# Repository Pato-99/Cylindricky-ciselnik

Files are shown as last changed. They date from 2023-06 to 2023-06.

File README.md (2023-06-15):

# Cylindrický číselník

Showcase

Mechanický cylindrický číselník je obdoba takzvaných "flip-clock" s tím,
že místo "flipujících" dlaždiček se otáčejí cylindry (válce). Díky tomu je možné
otáčet číselníkem na obě strany a také je ho možné umístit v jakékoliv poloze,
protože ke změně čísel není potřeba gravitace tak jako u "flip-clock".

## Klíčové vlastnosti

- modularita
- jednoduché rozhraní
- asynchronní ovládání jednotlivých válců

## Ovládání/Rozhraní

Číselník lze ovládat pomocí jednoduchých příkazů přes UART nebo MQTT

| Příkaz | Popis |
|---|---|
| `SHOW <int>` | Zobrazí dané číslo. Pokud je počet číslic větší než počet cylindrů, tak se ořízne zprava. |
| `SHOWF <float> <n>` | Zobrazí float na n desetinných míst. Případně se číslo ořízne zprava. |
| `INFO` | Vypíše info jaké číslo je právě zobrazováno a stavy motorů. |
| `CONFIGURE` | Spustí konfigurační mód. |

### Konfigurační mód

Pomocí posílání číslovek (`1, 2, 3, 4, 5, 6, ...`) se po jednotlivých krocích nastaví motory tak,
aby displej ukazoval samé nuly. Potom posláním `s` nastavení uložíme.

Nastavení je poté uloženo ve flash paměti zařízení a tak zůstává zachováno
i po rebootu.

## Implementace SW

K implementaci SW byl použit programovací jazyk MicroPython.

Program se skládá ze 2 hlavních částí:

1. Zpracování vstupu
2. Driver displeje/motorů

V samotné implementaci driveru byly použity 3 úrovně abstrakce.

1. Driver samotného unipolárního krokového motoru
2. Driver jednotlivých cylindrů (motor, převod, logika zobrazování číslic)
3. Driver displeje jako celku (skládá se z cylindrů)

### Asynchronní ovládání

Ovládání jednotlivých motorů je řešeno asynchronně pomocí knihovny `uasyncio`.

Asynchronní programování se hodí použít tam, kde jsou procedury takzvaně "I/O bound.
To znamená, že většinu času běhu procedury zabírá čekání například na vstup,
na navázání spojení atd. V našem případě je to čekání mezi jednotlivými kroky
krokového motoru. Myšlenkou je využití tohoto času pro něco užitečnějšího.
Díky tomu můžeme dosáhnout určité míry paralelismu za použití jen jednoho
vlákna.

Základem jsou klíčová slova `async` a `await`.

Připsáním klíčového slova `async` před deklaraci funkce říkáme, že se jedná
o takzvanou **courutine** a že se o její běh bude starat uasyncio. Coroutines 
je možné volat z jiných coroutines za použítí klíčového slova `await` nebo
předáním jako parametr funkcím z uasyncio knihovny (run(), gather()...).

**Asynchronní implementace otočení motoru o určitý počet kroků:**
```python
async def turn_steps(self, steps):
    reverse = False
    if steps < 0:
        reverse = True
        steps = -steps
    for _ in range(steps):
        self.step(reverse)
        await asyncio.sleep_ms(self.delay)
```

**Otáčení 3 cylindry naráz:**
```python
async def show(self, number):
    await asyncio.gather(
        self.digit2.show((number // 100) % 10),
        self.digit1.show((number // 10) % 10),
        self.digit0.show(number % 10)
    )
```

Zde funkce `asyncio.gather()` spustí otáčení všech 3 cylindrů naráz
a skončí až se dotočí poslední.

### MQTT

Původně bylo v plánu i ovládání přes MQTT přímo pomocí desky s WiFi čipem 
RPi Pico W, ale po testování se ukázalo, že tato metoda není úplně spolehlivá.
Vyskytovaly se časté výpadky spojení. Proto jsem napsal script, který běží na PC
a přes UART přeposílá příkazy z MQTT do připojeného RPi Pico.

## Konsktrukce

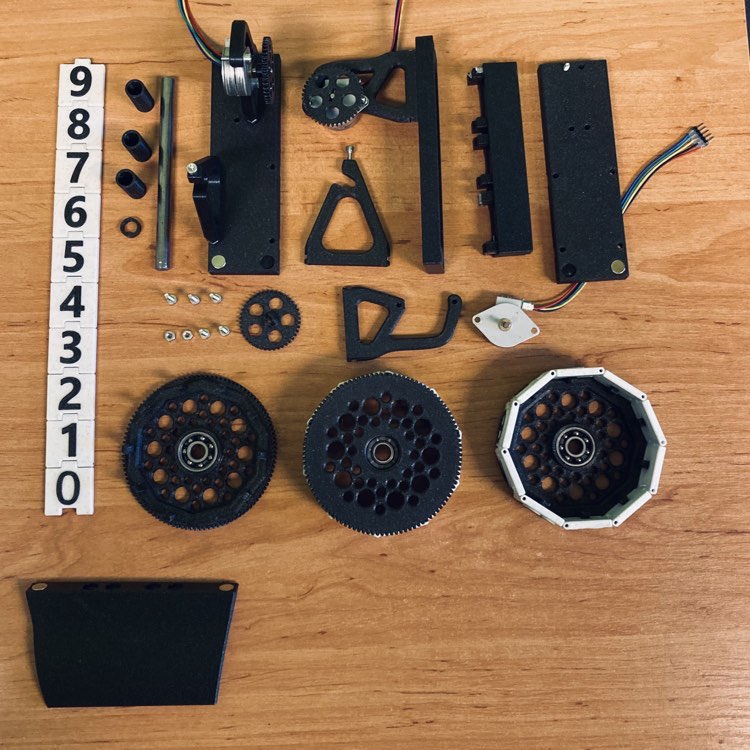
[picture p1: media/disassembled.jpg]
Disassembled


Při designu číselníku byl kladen důraz na to, aby byla konsktrukce co nejvíce modulární
a také aby se použily pouze běžně dostupné součástky. Díky tomu lze snadno postavit
číselník s libovolným počtem cylindrů.

### Použité součástky:

- RPi Pico
- tranzistorové pole ULN2004
- elektrolytické kondenzátory 44 uF
- krokové motory z AliExpressu řízené unipolárně

- šroub s válcovou hlavou s vnitřním šestihranem M3
- matice M3
- ložiska 608
- tyč D=8mm
- neodymové magnety

- 3D tištěné díly

## TODO

* implementace pro jednoduché zapojení libovolného počtu motorů
  pomocí **tuple unpacking**
* built-in mqtt
* upravit konsktrukci pro motory 28BYJ-48

## Užitečné odkazy

* [MicroPython](https://micropython.org/)
* [uasyncio](https://docs.micropython.org/en/latest/library/uasyncio.html)

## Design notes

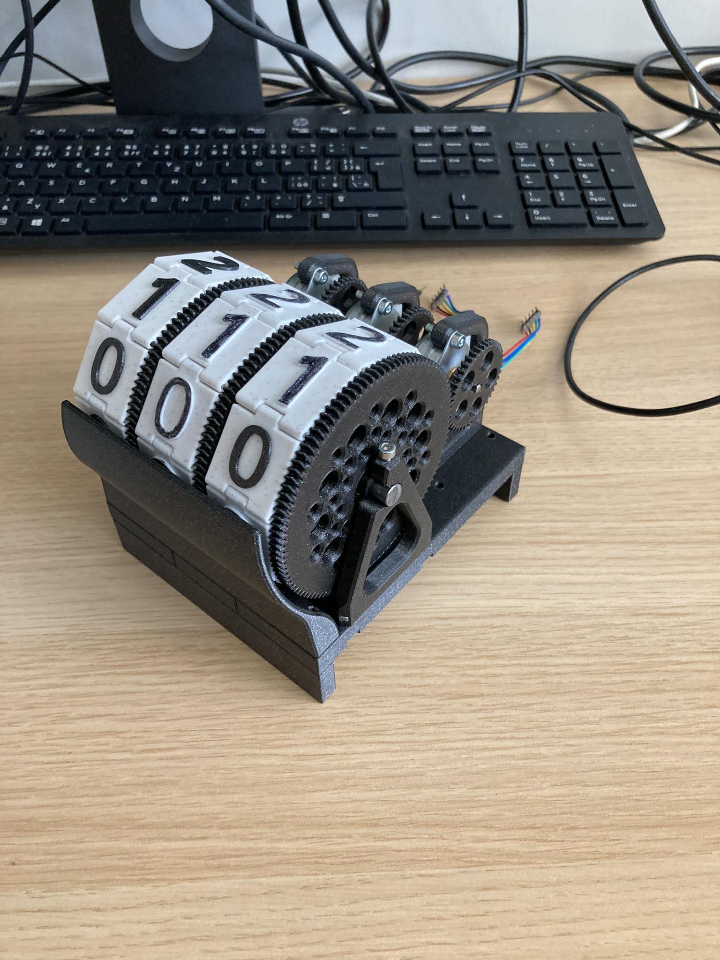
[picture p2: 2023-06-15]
media/overview.jpg

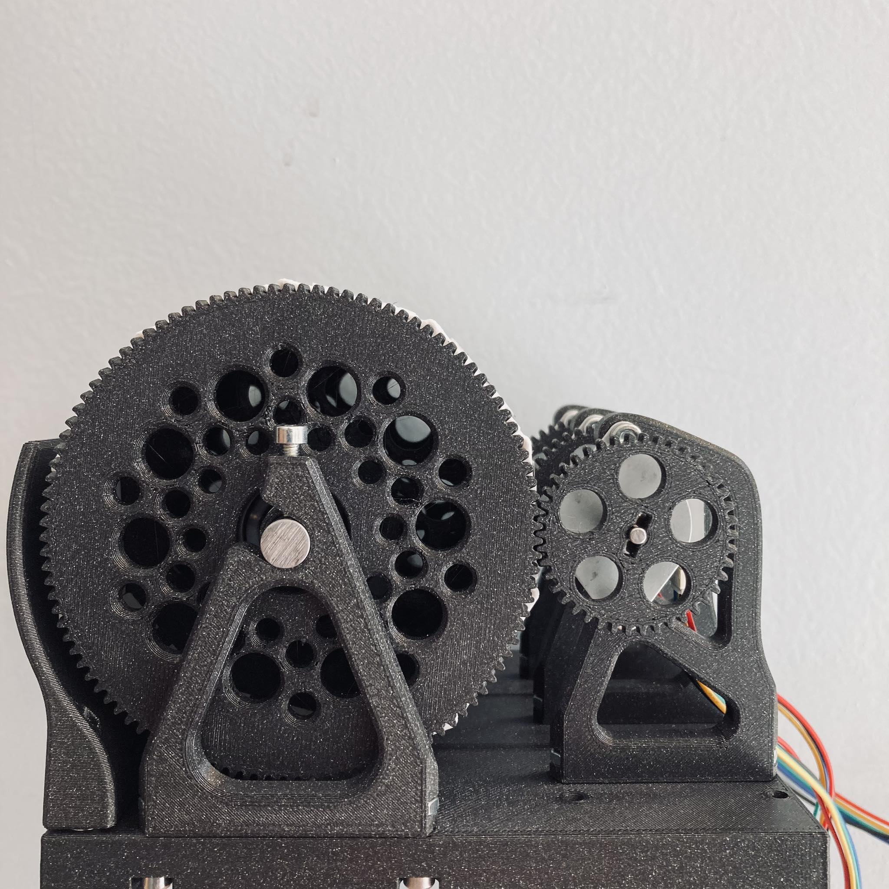
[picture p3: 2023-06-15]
media/sideview.jpg

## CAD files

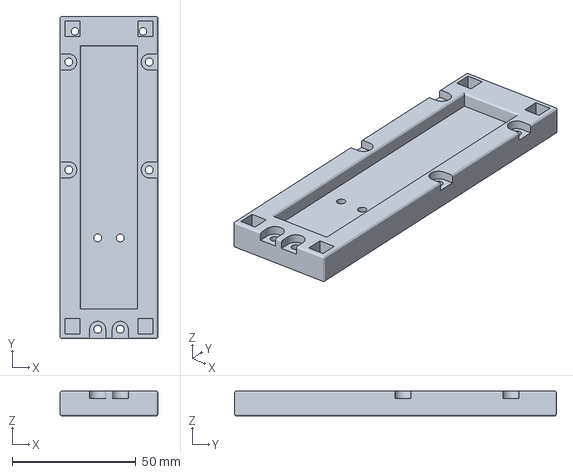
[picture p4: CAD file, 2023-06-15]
3d/base_side.3mf
39.5 x 130.0 x 10.0 mm

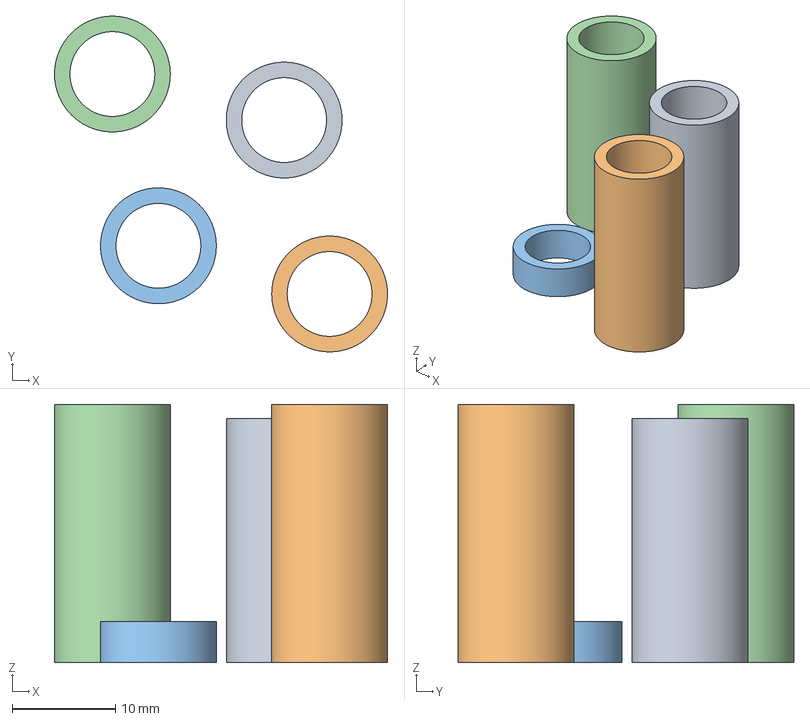
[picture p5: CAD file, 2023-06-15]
3d/spacers.3mf
32.2 x 32.5 x 25.0 mm

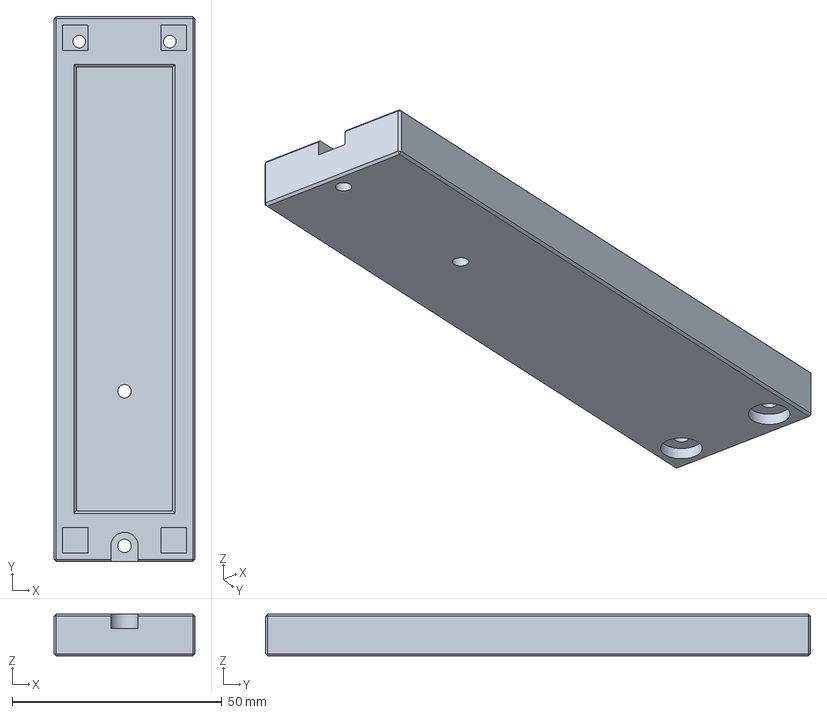
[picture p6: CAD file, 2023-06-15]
3d/base_mid.3mf
33.6 x 130.0 x 10.0 mm

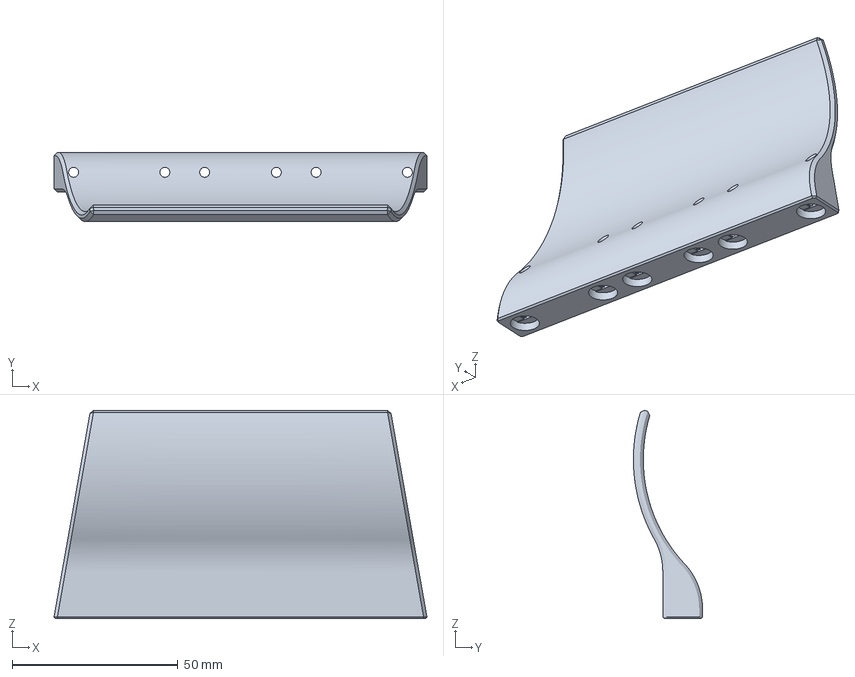
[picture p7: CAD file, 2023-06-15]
3d/cover.3mf
112.4 x 20.9 x 62.8 mm

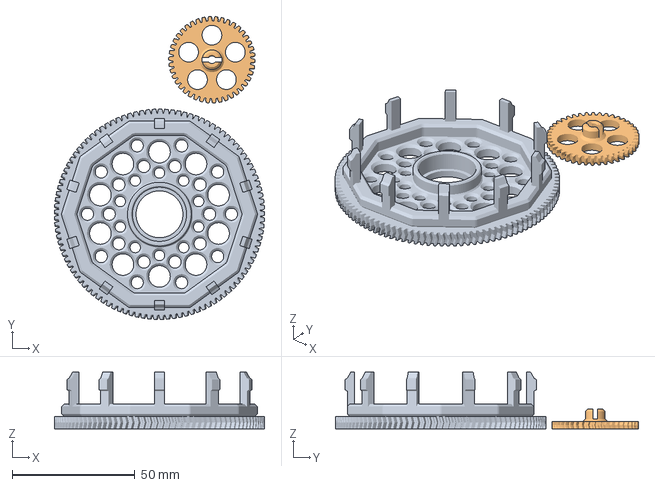
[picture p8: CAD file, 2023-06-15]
3d/gears.3mf
85.6 x 123.3 x 23.0 mm

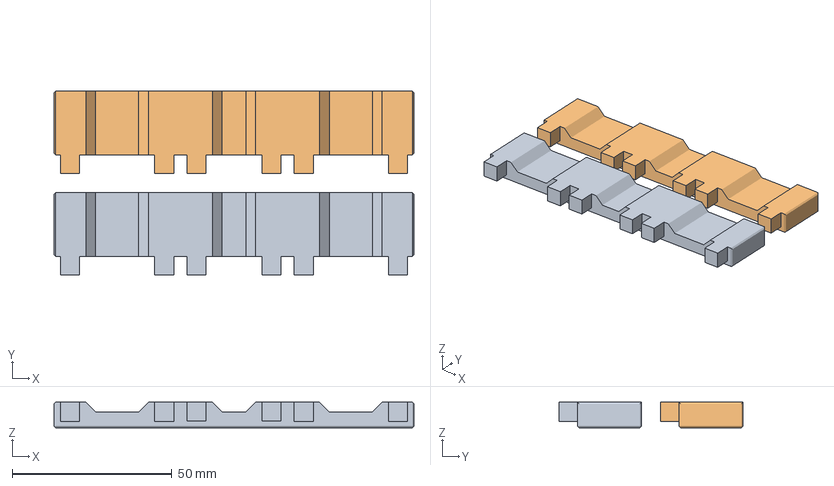
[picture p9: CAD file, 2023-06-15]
3d/base_legs.3mf
112.6 x 57.6 x 8.00 mm

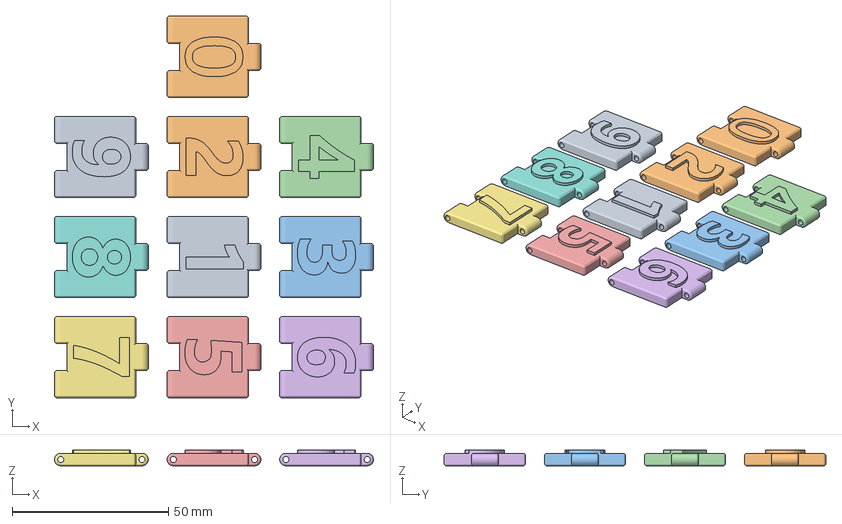
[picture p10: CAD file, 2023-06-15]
3d/numbers.3mf
102.0 x 122.0 x 5.00 mm

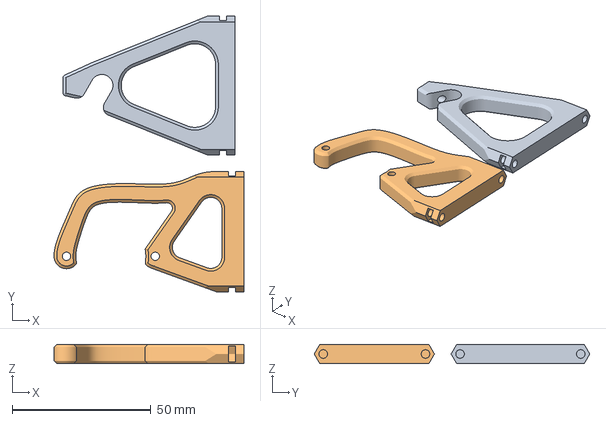
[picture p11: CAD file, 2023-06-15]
3d/holders.3mf
68.5 x 99.3 x 7.00 mm

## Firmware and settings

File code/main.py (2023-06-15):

import sys
# import network
import uasyncio as asyncio
from machine import Pin


class Stepper:
    sequence = [[1, 0, 0, 0],
                [1, 1, 0, 0],
                [0, 1, 0, 0],
                [0, 1, 1, 0],
                [0, 0, 1, 0],
                [0, 0, 1, 1],
                [0, 0, 0, 1],
                [1, 0, 0, 1]
                ]
    
    
    def __init__(self, p1, p2, p3, p4):
        self.state = 0
        self.step_angle = 375  # deg * 100
        self.min_delay = 8  # ms
        self.delay = 8 # ms
        self.pins = [Pin(p1, Pin.OUT),
                     Pin(p2, Pin.OUT),
                     Pin(p3, Pin.OUT),
                     Pin(p4, Pin.OUT)]
    
    def idle(self):
        for pin in self.pins:
            pin.off()
    
    def speed(self, s):
        self.delay = s * 1000 // self.step_angle
        
    def angle_to_steps(self, angle):
        return (angle * 100) // self.step_angle
    
    def step(self, reverse=False):
        increment = - 1 if reverse else 1
        self.state = (self.state + increment) % len(__class__.sequence)
        self.set_state(self.state)
    
    def set_state(self, state_number):
        for pin, state in zip(self.pins, __class__.sequence[state_number]):
            pin.value(state)
        
    async def turn_steps(self, steps):
        reverse = False
        if steps < 0:
            reverse = True
            steps = -steps
        for _ in range(steps):
            self.step(reverse)
            await asyncio.sleep_ms(self.delay)
    
    async def turn_angle(self, angle):
        await self.turn_steps(self.angle_to_steps(angle))


class Cylinder:
    def __init__(self, motor):
        self.current = 0
        self.one_step_angle = 36
        self.motor = motor
        self.ratio = 25  # ratio * 10
    
    async def show(self, number):
        diff1 = (number - self.current) % 10
        diff2 = (self.current - number) % 10
        
        diff = diff1
        if diff2 < diff1:
            diff = -diff2
        angle = diff * self.one_step_angle
        self.current = number
        await self.motor.turn_angle(angle * self.ratio // 10 * -1)
        
    def idle(self):
        self.motor.idle()
        
    def reset_state(self):
        self.current = 0
        
        
class Display:
    def __init__(self,  digit0, digit1, digit2):
        self.digit0 = Cylinder(digit0)
        self.digit1 = Cylinder(digit1)
        self.digit2 = Cylinder(digit2)
        self.state_file = "state.txt"
    
    async def show(self, number):
        await asyncio.gather(
            self.digit2.show((number // 100) % 10),
            self.digit1.show((number // 10) % 10),
            self.digit0.show(number % 10)
        )
        
    async def showf(self, number, decimal):
        await self.show(int(number * 10 ** decimal))
        
    async def countdown(self, number):
        await self.show(number)
        await asyncio.sleep_ms(1000)
        
        for i in range(number):
            await self.show(number - i - 1)
            await asyncio.sleep_ms(1000)
        
    def load_state(self):
        with open(self.state_file, "r") as file:
            state = file.readline().split(",")
            self.digit2.current = int(state[0])
            self.digit2.motor.state = int(state[1])
            self.digit1.current = int(state[2])
            self.digit1.motor.state = int(state[3])
            self.digit0.current = int(state[4])
            self.digit0.motor.state = int(state[5])
    
    def save_state(self):
        with open(self.state_file, "w") as file:
            file.write(f"{self.digit2.current},{self.digit2.motor.state}, {self.digit1.current},{self.digit1.motor.state},{self.digit0.current},{self.digit0.motor.state}")
            
    def reset_state(self):
        self.digit1.reset_state()
        self.digit0.reset_state()
        self.save_state()
    
    def idle(self):
        self.digit1.idle()
        self.digit0.idle()
        
    async def start(self):
        """
        Control interface commands
        
        SHOW (int)          - displays integer, truncates from left
        SHOWF (float) (n)   - displays float with (n) digits after floating point, truncates from left
        CONFIGURE           - start the configuration mode
        """
        reader = asyncio.StreamReader(sys.stdin)
        while True:
            command_raw = await reader.readline()
            #print(command_raw)
            command_parts = command_raw.decode().split()
            
            
            try:
                command = command_parts[0].upper()
            except IndexError:
                continue
            
            #print(command_parts)
            
            if command == "SHOW":
                try:
                    await self.show(int(command_parts[1]))
                except:
                    print("Value is not a number")
            elif command == "SHOWF":
                try:
                    await self.showf(float(command_parts[1]), int(command_parts[2]))
                except:
                    print("Value is not a number")
            elif command == "COUNTDOWN":
                try:
                    print(f"Countdown from {int(command_parts[1])}")
                    await self.countdown(int(command_parts[1]))
                except:
                    print("Value is not a number")
            elif command == "INFO":
                print(self)
            elif command == "SAVE":
                self.save_state()
                print("State saved")
            elif command == "SET":
                self.digit0.current = int(command_parts[1]) % 10
                self.digit1.current = (int(command_parts[1]) // 10) % 10
                self.digit2.current = (int(command_parts[1]) // 100) % 10
                print(self)
            elif command == "CONFIGURE":
                print("CONFIGURATION started")
                while True:
                    command = await reader.read(1)
                    #print(type(command), command)
                    if command == "1":
                        self.digit0.motor.step()
                    elif command == "2":
                        self.digit0.motor.step(reverse=True)
                    elif command == "3":
                        self.digit1.motor.step()
                    elif command == "4":
                        self.digit1.motor.step(reverse=True)
                    elif command == "5":
                        self.digit2.motor.step()
                    elif command == "6":
                        self.digit2.motor.step(reverse=True)
                    elif command == "s":
                        self.reset_state()
                        self.save_state()
                        print("Display configuration success")
                        break
                    await asyncio.sleep_ms(30)
                
    
    def __repr__(self):
        r = "Display\n"
        r += f"\tDisplayed number: {self.digit2.current}{self.digit1.current}{self.digit0.current}\n"
        r += f"\tMotor states: {self.digit2.motor.state}, {self.digit1.motor.state}, {self.digit0.motor.state}\n"
        return r


# async def connect(ssid, psk):
#     #Connect to WLAN
#     wlan = network.WLAN(network.STA_IF)
#     wlan.active(True)
#     wlan.connect(ssid, psk)
#     for _ in range(10):
#         if wlan.isconnected():
#             break
#         print('Waiting for connection...')
#         asyncio.sleep_ms(3000)
#     else:
#         print("Cannot connect to network. Resetting...")
#         machine.reset()
    
#     ip = wlan.ifconfig()[0]
#     print(f'Connected to {ssid} on {ip}')
#     return ip


async def main():
    try:
        display.load_state()
    except Exception as e:
        print(e)
    print(display)
    
    await display.start()

    
digit0 = Stepper(0, 1, 2, 3)
digit0.delay = 16
digit1 = Stepper(4, 5, 6, 7)
digit1.delay = 16
digit2 = Stepper(8, 9, 10, 11)
digit2.delay = 16
display = Display(digit0, digit1, digit2)


try:
    asyncio.run(main())
except:
    print("Exception occured. Saving state and exiting.")
    display.save_state()
    raise
    

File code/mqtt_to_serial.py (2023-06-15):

#!/usr/bin/env python3

import serial
import paho.mqtt.client as paho
from time import sleep

try:
    ser = serial.Serial("/dev/ttyACM0", 115200)
    sleep(0.1)
    ser.flushInput()
    print(ser.name)

    ser.write(b"SHOW 11\n")
    ser.write(b"SHOW 22\n")
    client = paho.Client()
    client.connect("mqtt.eclipseprojects.io")


    def on_message(mosq, obj, msg):
        print(msg.payload)
        ser.write(msg.payload + b"\n")
        ser.flush()

    client.on_message = on_message
    client.subscribe("nsi/display")

    client.loop_forever()


except Exception as e:
    print("Unable to open serial port")
    raise
